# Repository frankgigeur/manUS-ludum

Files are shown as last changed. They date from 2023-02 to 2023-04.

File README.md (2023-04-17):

# ManUS Ludum

### Main robotisée et vision AI | UdeS-GRO
 

## Présentation du projet
L’objectif du projet est de concevoir la portion mécanique, électrique et informatique d’une main robotisée anthropomorphique pouvant actionner ses doigts pour jouer à roche-papier-ciseau. Une caméra vient en support à la main pour rendre le jeu encore plus interactif et réaliste.

gif &nbsp; &nbsp;gif

Les membres de l'équipe sont : <strong>Audrey Guy</strong>, <strong>Nicolaï Boudjack</strong>, <strong>Charles Ouellet</strong> et <strong>Alex Miville Deschênes</strong>.

GetImage
GetImage (1)
GetImage (2)
GetImage (3)

## Téléchargement et démarrage du projet
Pour télécharger le projet, il vous suffit de cloner le répertoire sur votre machine

1. Cloner le projet et l'enregistrer sur votre machine


2. Suivre les étapes des différentes sections du projet

> Interface de jeux et vision

> Électrique

> Mécanique

## Table des matières
* [Mécanique](/Mécanique#manUS-ludum)
	* [Fichiers CAD](https://github.com/frankgigeur/manUS-ludum/tree/main/M%C3%A9canique/CAD)
	* [Comment fabriquer ...](https://github.com/frankgigeur/manUS-ludum/tree/main/M%C3%A9canique#documentation-m%C3%A9canique)
		* [Liste des matériaux et composantes](https://github.com/frankgigeur/manUS-ludum/tree/main/M%C3%A9canique#liste-des-mat%C3%A9riaux-et-composantes)
		* [Fabrication des composantes](https://github.com/frankgigeur/manUS-ludum/tree/main/M%C3%A9canique#fabrication-des-composantes)
		* [Assemblage mécanique](https://github.com/frankgigeur/manUS-ludum/tree/main/M%C3%A9canique#assemblage-m%C3%A9canique)
*  [Électrique](/Électrique#manUS-ludum)
	* [Liste des matériaux et composantes](https://github.com/frankgigeur/manUS-ludum/tree/main/%C3%89lectrique#liste-des-mat%C3%A9riaux-et-composantes)
	* [Assemblage électrique](https://github.com/frankgigeur/manUS-ludum/tree/main/%C3%89lectrique#assemblage-%C3%A9lectrique)
* [Interface](/Interface%20Jeux#manUS-ludum)
	* [Logiciels requis](/Interface%20Jeux/README.md#installation-des-logiciels-recommandés)
	* [Dépendances](/Interface%20Jeux/README.md#Consolidation-des-versions-et-des-dépendances)
	* [Code de l'interface](/Interface%20Jeux/README.md#Comment-démarrer-linterface)
	* [Code de communication](/Interface%20Jeux/README.md#Comment-fonctionne-la-communication)
* [Vision](/Interface%20Jeux#manUS-ludum)
	* [Matériel nécessaire](/Interface%20Jeux/README.md#Matériel-nécessaire)
	* [Code de la reconnaissance visuelle](/Interface%20Jeux/README.md#Comment-fonctionne-la-reconnaissance-visuelle)
* [Arduino](https://github.com/frankgigeur/manUS-ludum/tree/main/Arduino/controle_servo)
* [Licence](/README.md#L43)

### Licence MIT
Copyright 2023 ManUS ludum

Permission is hereby granted, free of charge, to any person obtaining a copy of this software and associated documentation files (the "Software"), to deal in the Software without restriction, including without limitation the rights to use, copy, modify, merge, publish, distribute, sublicense, and/or sell copies of the Software, and to permit persons to whom the Software is furnished to do so, subject to the following conditions:

The above copyright notice and this permission notice shall be included in all copies or substantial portions of the Software.

THE SOFTWARE IS PROVIDED "AS IS", WITHOUT WARRANTY OF ANY KIND, EXPRESS OR IMPLIED, INCLUDING BUT NOT LIMITED TO THE WARRANTIES OF MERCHANTABILITY, FITNESS FOR A PARTICULAR PURPOSE AND NONINFRINGEMENT. IN NO EVENT SHALL THE AUTHORS OR COPYRIGHT HOLDERS BE LIABLE FOR ANY CLAIM, DAMAGES OR OTHER LIABILITY, WHETHER IN AN ACTION OF CONTRACT, TORT OR OTHERWISE, ARISING FROM, OUT OF OR IN CONNECTION WITH THE SOFTWARE OR THE USE OR OTHER DEALINGS IN THE SOFTWARE.

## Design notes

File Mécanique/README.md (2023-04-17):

# Documentation-Mécanique

## Fichiers ['CAD'](./CAD/)
Les fichiers suivants contiennent les CAD nécessaires à la ['fabrication'](##Fabrication%20des%20composantes) des composantes mécaniques du projet.

- [ ]  [`Doigts`](./CAD/Doigts/), [`Paume`](./CAD/Paume%20et%20poignet//), [`Poignet`](./CAD/Paume%20et%20poignet//) <br>
- [ ]  [`Ligaments`](./CAD/Ligaments/) <br>
- [ ]  [`Support moteur`](./CAD/Moteurs%20support%20et%20poulies/), [`Poulies moteurs`](./CAD/Moteurs%20support%20et%20poulies/) <br>
- [ ]  [`Support arbre`](./CAD/M%C3%A9canisme%20redirection%20fils/), [`Poulies arbre`](./CAD/M%C3%A9canisme%20redirection%20fils/), [`Support supérieur`](./CAD/M%C3%A9canisme%20redirection%20fils/) <br>
- [ ]  [`Base`](./CAD/Plaque%20montage/) <br>

## Liste des matériaux et composantes
- [ ] &nbsp;Vis autoperçantes M1.2 x 3mm <br>
- [ ] &nbsp;Vis M3 x 20mm <br>
- [ ] &nbsp;Vis M3 x 45mm <br>
- [ ] &nbsp;Vis M5 x 10mm <br>
- [ ] &nbsp;Vis M5 x 50mm <br>
- [ ] &nbsp;12 x 12 x 1/8 po. Acrylique <br>
- [ ] &nbsp;Feuille de nylon cordura 1000D [(Club Tissu)](https://www.clubtissus.com/fr/nylon-cordura-1000d-noir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) <br>
- [ ] &nbsp;Mica plastique transparent 20 ga (Club Tissu) <br>
- [ ] &nbsp;Aggraphe à papier <br>
- [ ] &nbsp;Arbre de métal 5mm x 100mm [(Amazon)](https://www.amazon.ca/dp/B01B27MJC6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) <br>
- [ ] &nbsp;Bearing à billes 5mm x 11mm x 4mm [(Amazon)](https://www.amazon.ca/dp/B07GBTWLCZ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) <br>
- [ ] &nbsp;Fil de pêche 80 lbs <br>
- [ ] &nbsp;Goupille (dowel pin) 1/8 x 0.5 po. <br> 
- [ ] &nbsp;Servomoteur HS-422 Hitec [(Robotshop)](https://ca.robotshop.com/fr/products/hitec-hs-422-servo-motor) <br>

## Fabrication des composantes
avant bras v1

La fabrication des composantes du projet nécessite l'accès à **une découpeuse laser**, **une imprimante 3D** et d'un **fer à souder**. 
Les étapes suivantes permmettent de fabriquer l'ensemble des composantes mécaniques du projets selon les étapes suivantes:

1. Impression des doigts du dossier [`Doigts`](./CAD/Doigts/) en PLA à l'aide d'une imprimante 3D (Infill minimum 80%).

2. Impression de la paume et de son support de type poignet dans le dossier [`Paume et poignet`](./CAD/Paume%20et%20poignet//) (Infill minimum 40%).

3. Impression des [`poulies de servo moteurs`](./CAD/Moteurs%20support%20et%20poulies/)  ( **x5** ), du [`support à moteurs`](./CAD/Moteurs%20support%20et%20poulies/), des [`poulies inserés sur les paliers à billes`](./CAD/M%C3%A9canisme%20redirection%20fils/) ( **x12** ) et des [`supports à arbre types 1 et 2`](./CAD/M%C3%A9canisme%20redirection%20fils/) ( **x4 chaque** ).

4. Découpe du [`support supérieur de la main`](./CAD/M%C3%A9canisme%20redirection%20fils/) en acrylique à l'aide d'une découpeuse laser.

4. Découpe des [`ligaments`](./CAD/Ligaments/) en nylon des différents doigts ( **2 par doigts** ) à l'aide de la découpeuse laser.

5. Découpe des [`ligaments`](./CAD/Ligaments/) en mica des différents doigts ( **3 par doigts** ) à l'aide de ciseaux.

6. Découpe des fils de pêche ≈ 60cm ( **x10** ).

7. Découpe de la [`base`](./CAD/Plaque%20montage/) en acrylique du support de la main à l'aide d'une découpeuse laser. 

## Assemblage mécanique
Pour l'assemblage des pièces mécaniques, se fier aux [`assemblages complets`](./CAD/Assemblages%20complets/) fournis ainsi qu'aux [`dessins`](./Dessins/), [images](https://github.com/frankgigeur/manUS-ludum/tree/main/Images) fournies et explications ultérieures.

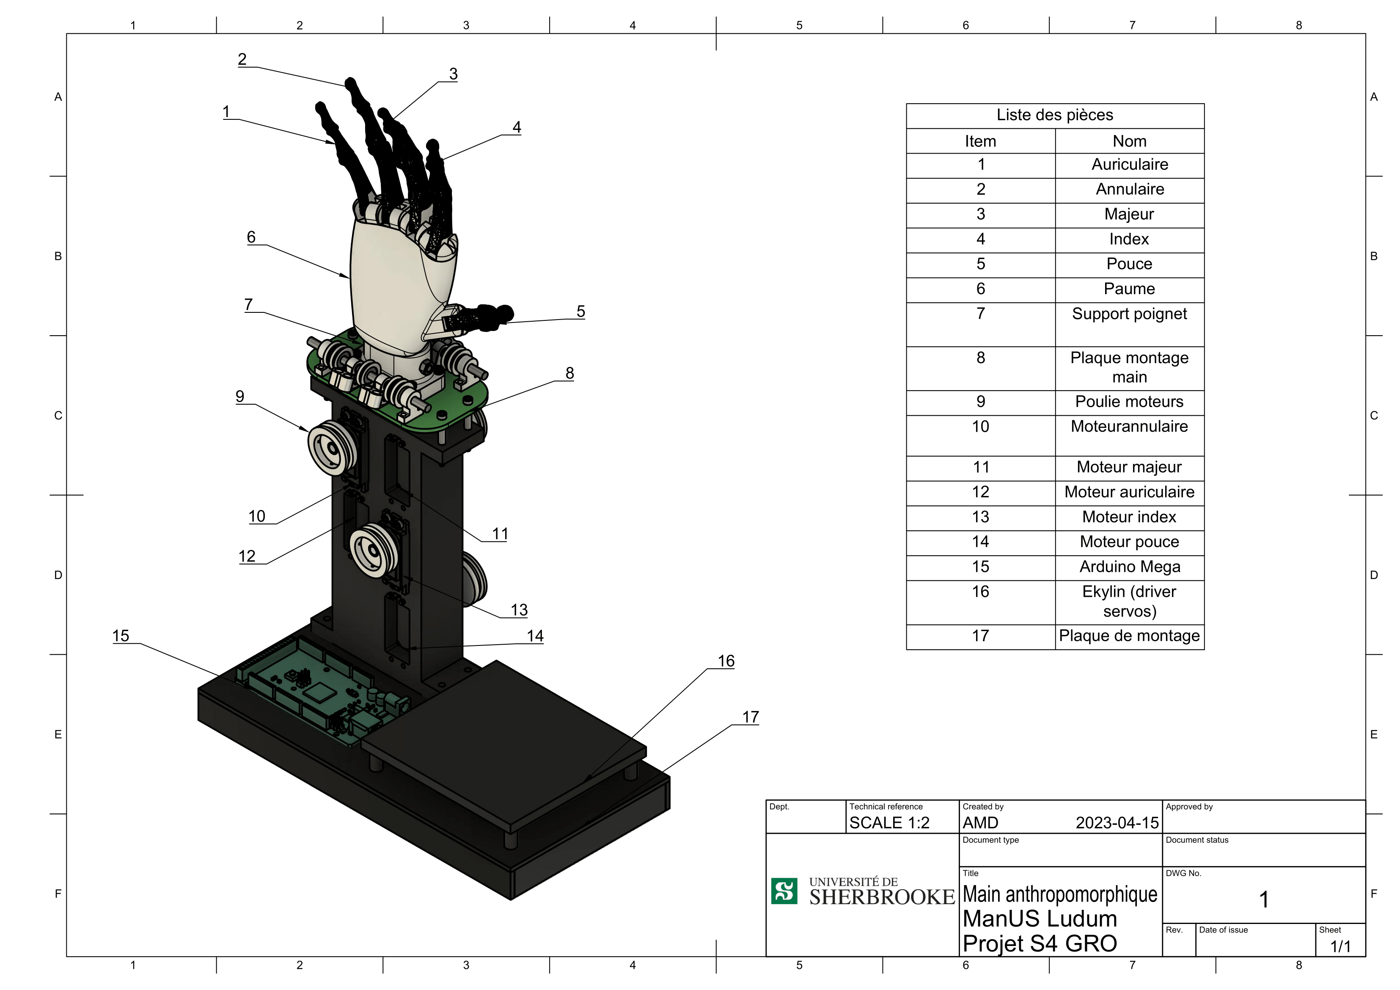
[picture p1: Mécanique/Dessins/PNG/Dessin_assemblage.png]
Dessin assemblage


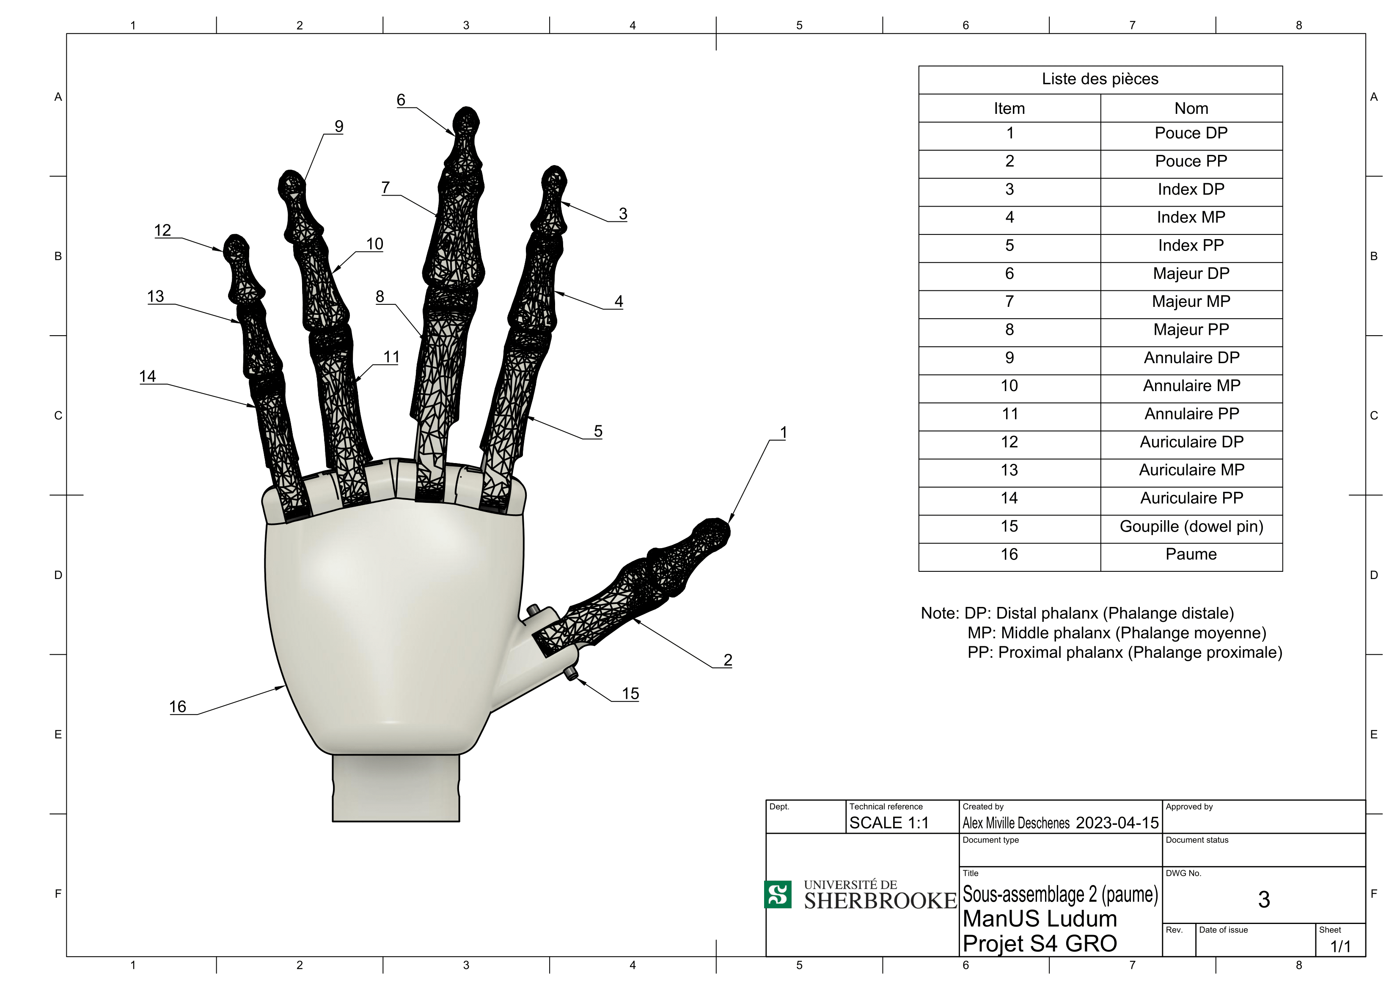
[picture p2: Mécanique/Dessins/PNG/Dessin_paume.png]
Dessin paume


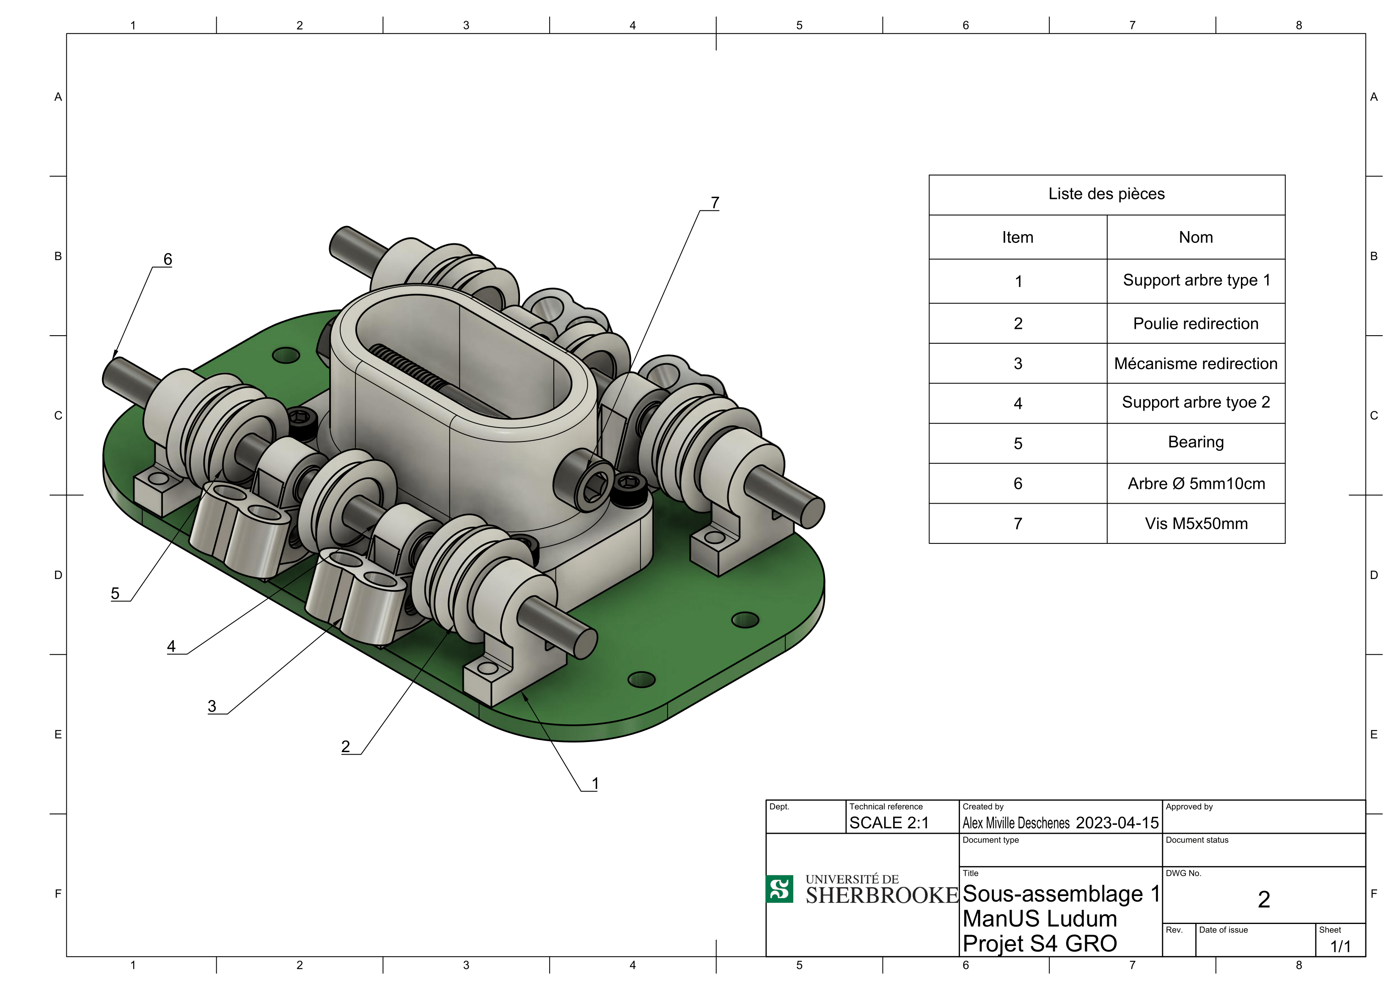
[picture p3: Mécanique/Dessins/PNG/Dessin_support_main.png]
Dessin redirection fils


### **Montage des doigts**
Pour le montage des doigts, il est nécesaire d'insérer les ligamants aux points d'insertion anatomique selon la figure suivante:
exemple ligament

Pour se faire, faire fondre les vis m1.2 aux points cibles et visser par la suite celles-ci avec les ligaments de mica et de nylon. La figure suivante présente le nom des ligaments à utiliser selon la jonction entre les ossements.

nom ligaments

La jonction MCPP est une superposition de ligaments de mica et de nylon, tandis que la jonction PPMP est seulement un ligament de nylon. Aussi, à noter que cette figure présente le montage de l'index, mais la même procédure s'applique pour tous les autres doigts. <br> <br>

Finalement, les poulies et les tendons peuvent être installés. Les aggraphes peuvent donc être pliées et coupées pour ensuite être insérées dans le doigt à l'aide d'un fer à souder. La figure suivante présente le positionnement des poulies (voir la section [Montage des poulies sur la paume](#montage-des-poulies-sur-la-paume))

### Montage des doigts sur la paume
Une fois les doigts assemblés, il faut les placer sur la paume. Pour se faire, on glisse la goupille (dowel pin) dans le trou situé sur la phalange proximale du doigt de manière à ce que celle-ci dépasse également de chaque côté.

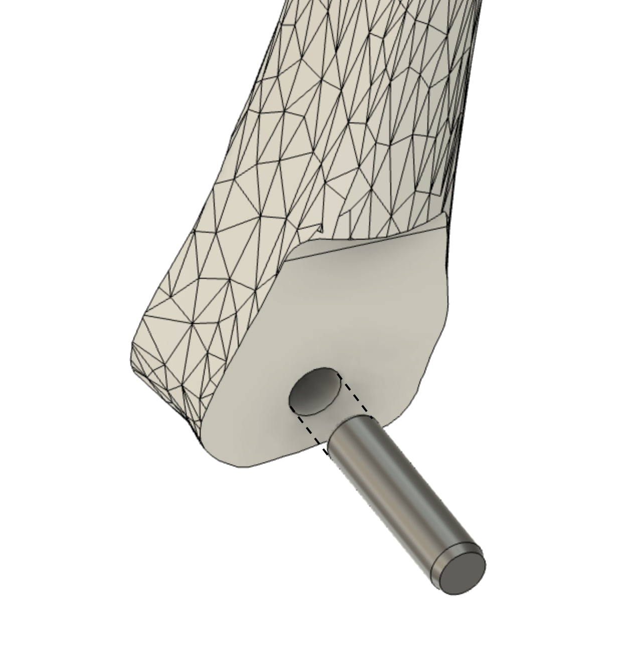
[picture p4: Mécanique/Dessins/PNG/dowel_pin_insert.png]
dowel insert


Ensuite, on force le doigt avec la goupille dans chacune des positions de la paume pour les doigts correspondants. Une grande force pourrait être nécessaire.

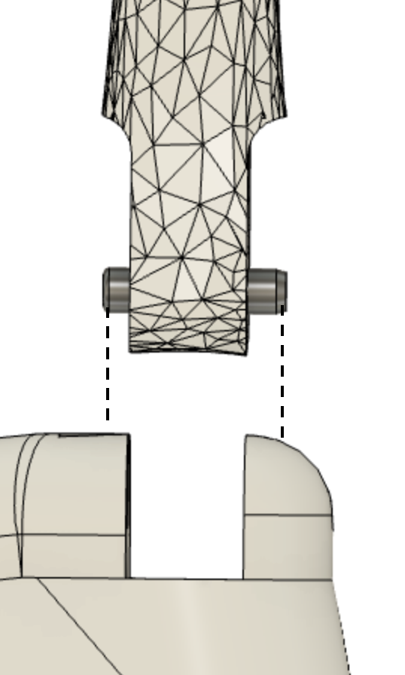
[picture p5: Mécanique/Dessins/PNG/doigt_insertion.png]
finger insert


### Montage des poulies sur la paume

Se fier à l'image suivante pour le montage des poulies de redirection des fils (agrafes à papier) sur la paume ainsi que le point de départ du fil de pêche:

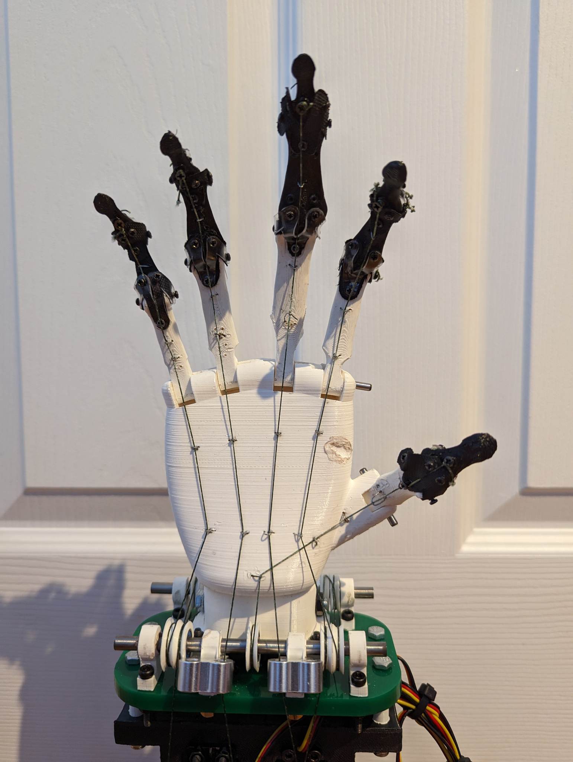
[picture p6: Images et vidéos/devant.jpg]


### Redirection des fils

Une fois la main assemblée et les poulies installées, il faut rediriger le fil de pêche vers les servomoteurs. La figure suivante montre la redirection du fil pour le petit doigt. Les flèches rouges sont associés au fil du devant et les flèches bleues au fil du derrière. De plus, le fil est enroulé une fois autour des poulies pour s'assurer qu'il ne sorte pas lors du mouvement.
CDhd5bslpE


Il est à noté que la redirection des fils de chaque doigt suit le même modèle que celui du petit doigt. Il suffit alors de reproduire pour chaque doigt.

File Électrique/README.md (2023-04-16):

# Documentation ManUS Ludum - Électrique

## Liste des matériaux et composantes
- [ ] &nbsp;Arduino Mega 2560  [(Arduino)](https://ca.robotshop.com/fr/products/hitec-hs-422-servo-motor) <br>
- [ ] &nbsp;Module PCA9685 [(Adafruit)](https://learn.adafruit.com/16-channel-pwm-servo-driver?view=all) <br>
- [ ] &nbsp;Connecteurs mâle-femelle type "jumper" (**x4**) <br>
- [ ] &nbsp;Alimentation 12V <br>
- [ ] &nbsp;Câble USB type A/B <br>

## Assemblage électrique
L'assemblage électrique du projet se résume aux étapes suivantes en se basant sur le schéma électrique suivant : 

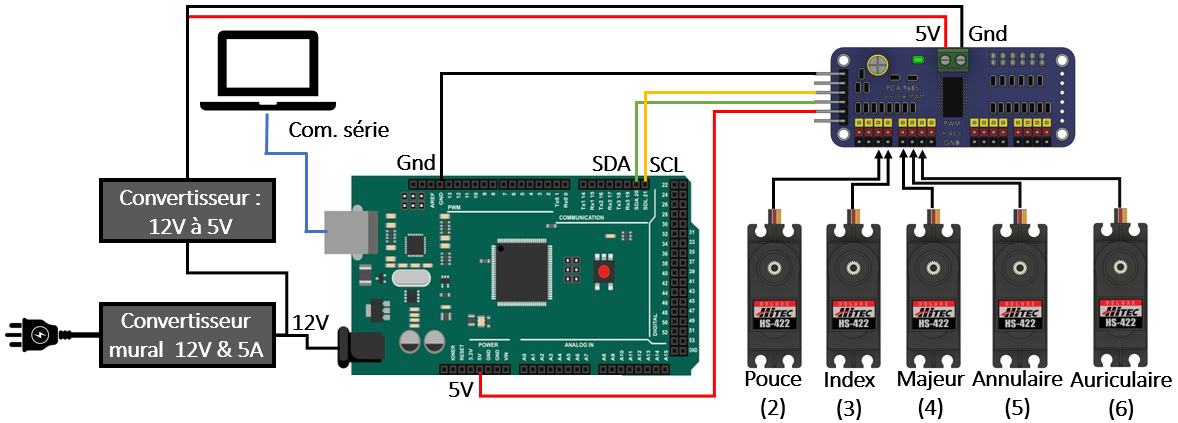
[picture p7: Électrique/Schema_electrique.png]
Schema electrique


1. Connecter les fils 5V, GND, SDA, SCL de l'Arduino au module PCA9685 selon le schéma ci-haut à l'aide des connecteurs mâle-femelle.

2. Connecter les fils des servomoteurs au module PCA9685 selon le schéma électrique en s'assurant de les placer dans le bon sens (bien regarder que le fil noir du servomoteur soit connecté au GND du module).

3. Connecter le convertisseur 12V à 5V au module PCA9685 toujours selon le schéma électrique.

4. Connecter l'alimentation 12V au Arduino et au convertisseur 12V à 5V.

5. Connecter le câble USB type A/B au Arduino ainsi qu'à l'ordinateur.

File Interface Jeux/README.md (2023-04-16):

# Documentation-Interface

# Matériel nécessaire
- [ ] Caméra (intégré à un ordinateur portable ou une webcam)
- [ ] ArduinoMEGA 2560

# Installation des logiciels recommandés
- [ ] PyCharm
 ```
 https://www.jetbrains.com/pycharm/download/#section=windows
 ```
- [ ] QtDesigner
 ```
 https://build-system.fman.io/qt-designer-download
 ```

# Consolidation des versions et des dépendances
Ce projet fonctionne avec Python 3.7 ou 3.10, mais il est bon de noter que les dépendances décrites ci-dessous s'appliquent à un environnement python 3.10.

## Installation des librairies et interpréteur
Pour commencer, installez python sur votre machine.
Ensuite, dans PyCharm, vous allez ajouter les librairies nécessaires à votre interpréteur en vous fiant aux étapes suivantes:

1. À partir de l'onglet "File" sélectionner "Settings"

2. Sous "Projet", sélectionner "Python Interpreter"

3. Choisir la version de python sur laquelle vous souhaitez installer vos librairies
 
4. En appuyant sur le bouton +, choissisez les librairies selon les requis énumérés ci-dessous et cliquez sur "Install Package"


## Liste des librairies à installer
- [ ] opencv-contrib-python == 4.3.0
- [ ] scikit-learn == 0.11
- [ ] tensorflow == 2.2.0
- [ ] numpy == 1.18.3
- [ ] matplotlib == 3.1.0
- [ ] scipy == 1.4.1
- [ ] PyQt5 == 5.15.9

S'il y a des erreurs de compilation, fiez-vous aux messages d'erreurs de la console et installez les librairies manquantes!

# Comment démarrer l'interface
Pour lancer et ou modifier l'interface, le fichier de code est InterfaceJeux.py .
Pour démarrer l'interface il suffit, dans PyCharm, d'appuyer sur le bouton "Run".



L'interface comprends des boutons de contrôle de la main, une rétroaction temps réel de la caméra, un décompte de jeux et des statistiques.



# Comment fonctionne la reconnaissance visuelle
Pour entraîner un nouveau modèle de reconnaissance visuelle, utilisez le fichier /ModeleVision/modelTraining.py .
Dans ce fichier, en vous fiant aux commentaires, vous serez en mesure de changer les différents paramètres du modèle
et d'entraîner votre propre modèle. Ensuite, dans le fichier algoRPC du dossier principal, vous n'aurez qu'à changer 
le nom du modèle à télécharger et à vous assurer que le dit modèle se trouve dans le dossier.



# Comment fonctionne l'algorithme décisionnel de jeux
De base, l'ordinateur jouera des coups aléatoires. Cependant, il est possible de le faire jouer avec un algorithme décisionnel
de type chaînes de Markov. Le code responsable des calculs statistiques derrrière les prédictions des chaînes est dans le fichier RPCmarkov.py

# Comment fonctionne la communication
La communication entre l'ordinateur et le microcontrôleur Arduino se fait par série avec le fichier CommWorker.py
Ce code produit une rétroaction à la console permettant à l'utilisateur de comprendre les commandes envoyées à la main.



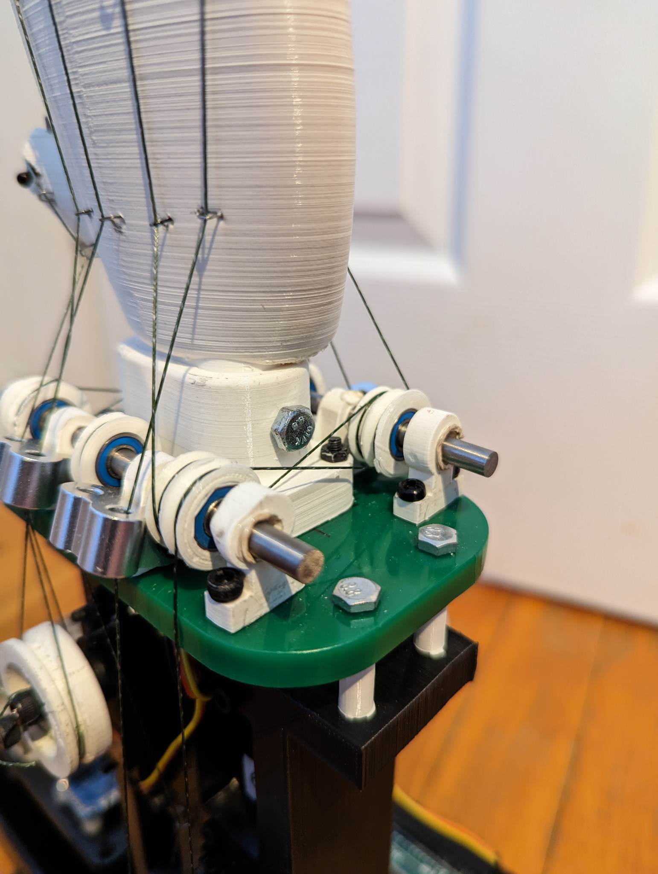
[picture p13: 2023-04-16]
Images et vidéos/poulies_redirection.jpg

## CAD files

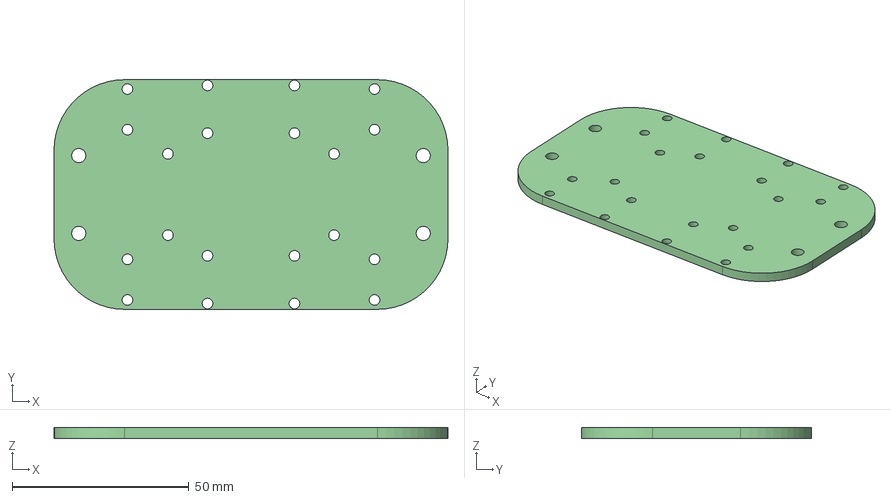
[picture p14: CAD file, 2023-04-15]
Mécanique/CAD/Mécanisme redirection fils/Plaque_montage_main.step
111.5 x 65.0 x 3.00 mm

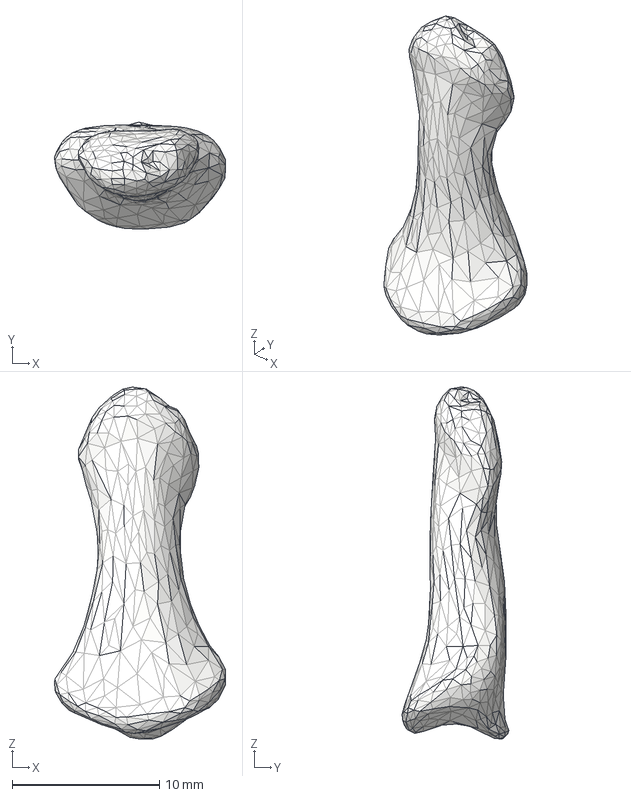
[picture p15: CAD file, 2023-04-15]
Mécanique/CAD/Doigts/Annulaire/STEP/Annulaire_DP.step
11.6 x 7.27 x 23.9 mm

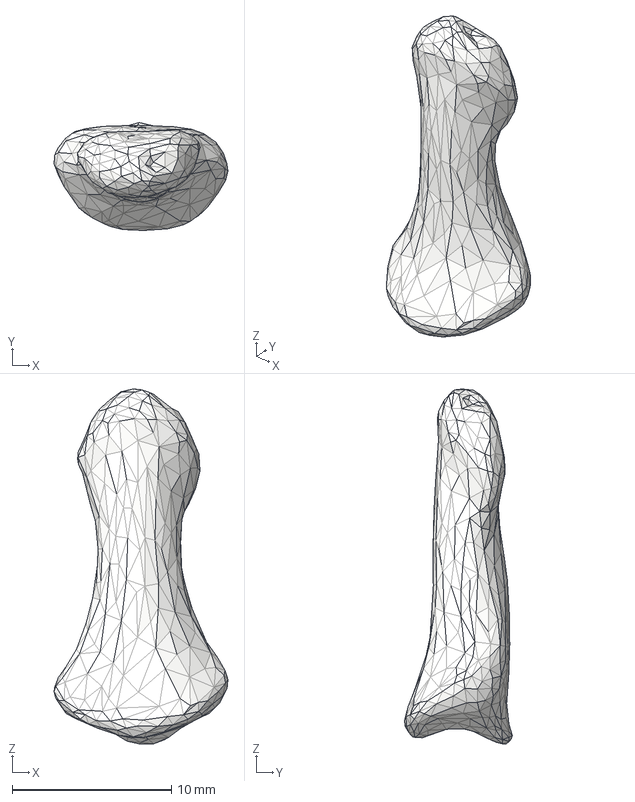
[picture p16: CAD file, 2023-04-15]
Mécanique/CAD/Doigts/Auriculaire/STEP/Auriculaire_DP.step
10.9 x 6.78 x 22.3 mm

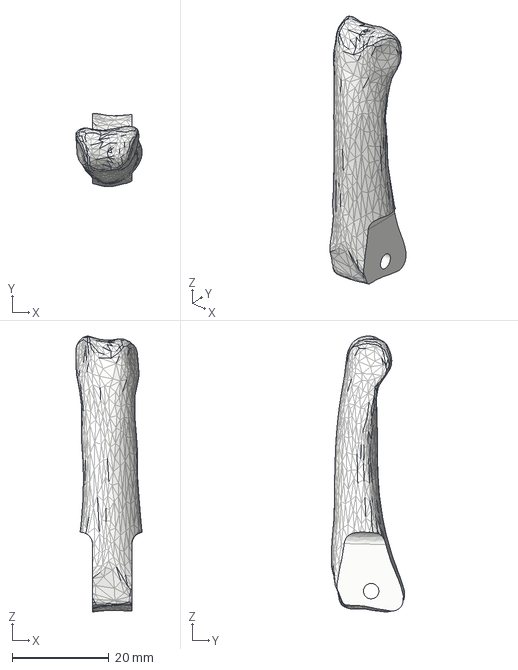
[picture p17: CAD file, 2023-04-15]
Mécanique/CAD/Doigts/Index/STEP/IndexPP.step
13.6 x 15.2 x 56.9 mm

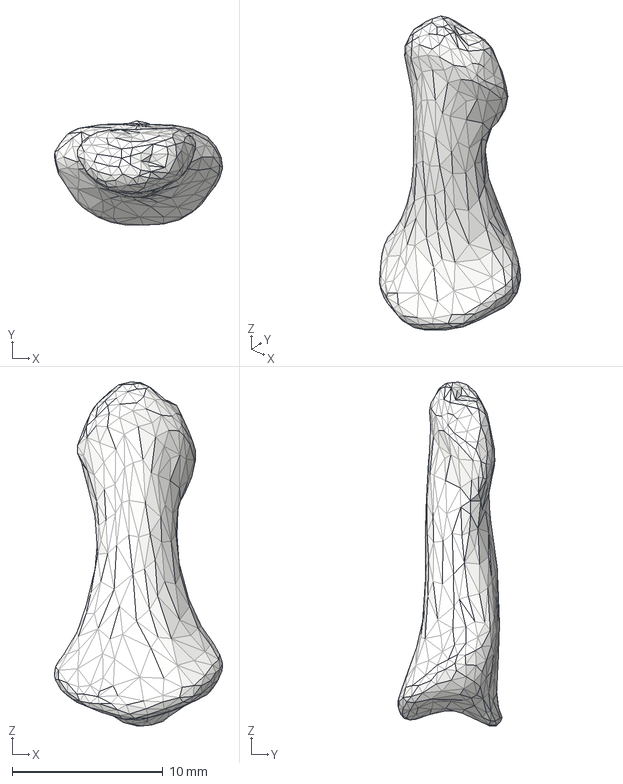
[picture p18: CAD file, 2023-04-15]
Mécanique/CAD/Doigts/Majeur/STEP/Majeur_DP.step
11.2 x 6.93 x 22.8 mm

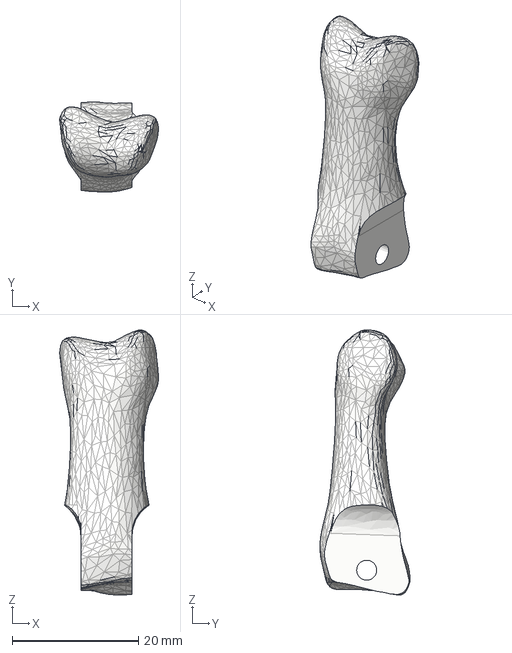
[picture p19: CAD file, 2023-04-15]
Mécanique/CAD/Doigts/Pouce/STEP/Pouce_PP.step
15.7 x 14.3 x 42.0 mm

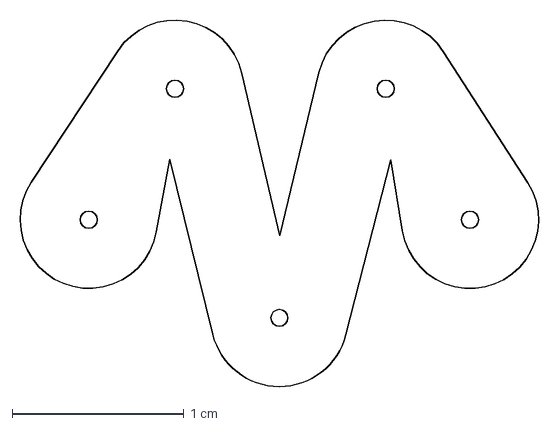
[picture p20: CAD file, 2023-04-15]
Mécanique/CAD/Ligaments/Universal DPMP Ligament.dxf
3.07 x 2.16 cm

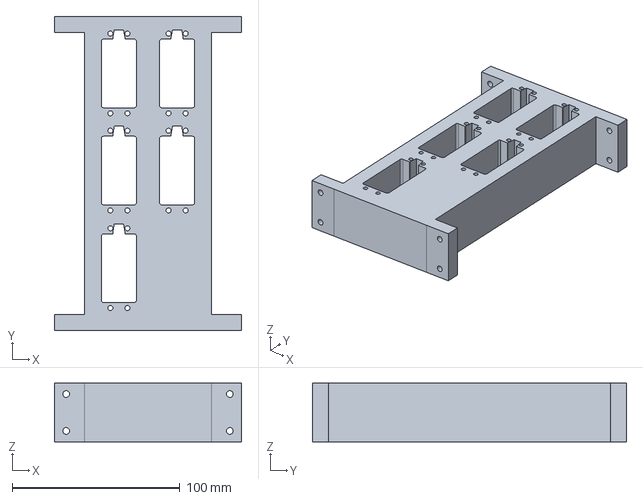
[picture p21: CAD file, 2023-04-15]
Mécanique/CAD/Moteurs support et poulies/Support_moteurs.step
111.5 x 187.0 x 35.0 mm

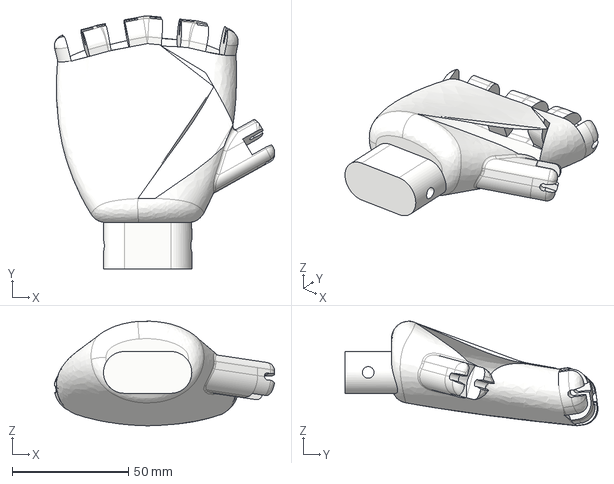
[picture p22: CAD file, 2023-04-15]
Mécanique/CAD/Paume et poignet/Paume.step
95.0 x 109.0 x 45.1 mm

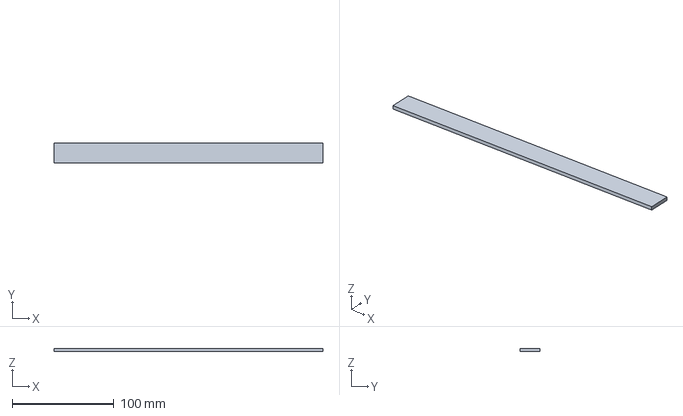
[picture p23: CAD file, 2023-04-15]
Mécanique/CAD/Plaque montage/Plaque_montage_devant_arriere.step
265.0 x 20.0 x 3.17 mm

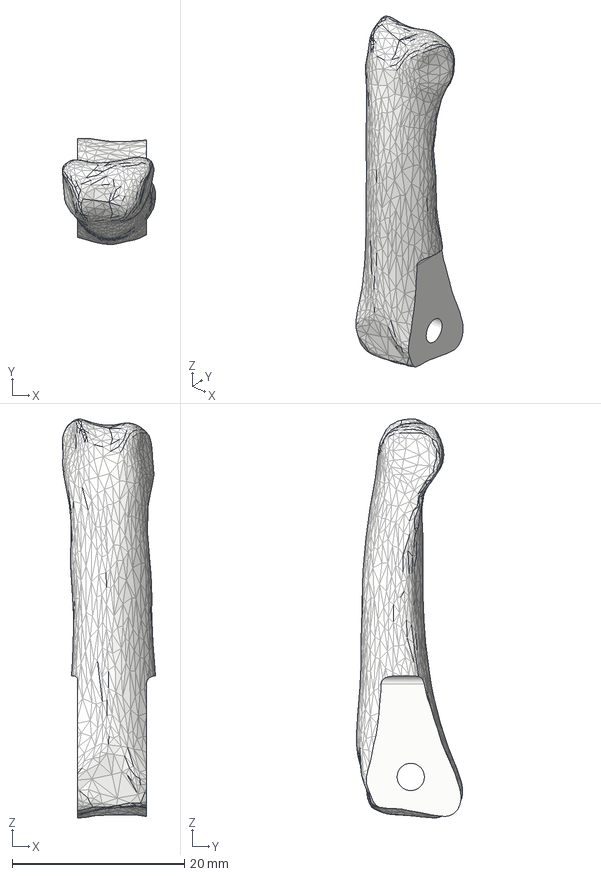
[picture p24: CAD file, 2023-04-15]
Mécanique/CAD/Doigts/Auriculaire/STEP/Auriculaire_PP.step
10.8 x 12.3 x 46.3 mm

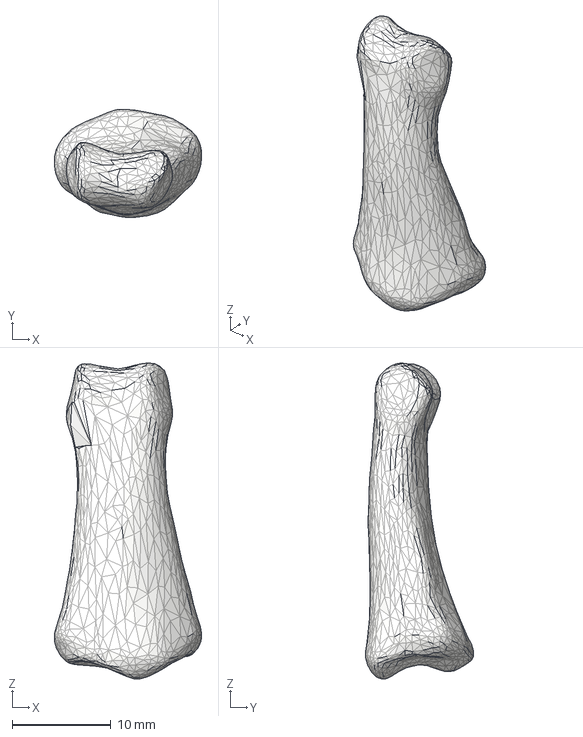
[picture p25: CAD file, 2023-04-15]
Mécanique/CAD/Doigts/Index/STEP/IndexMP.step
15.0 x 11.0 x 32.1 mm

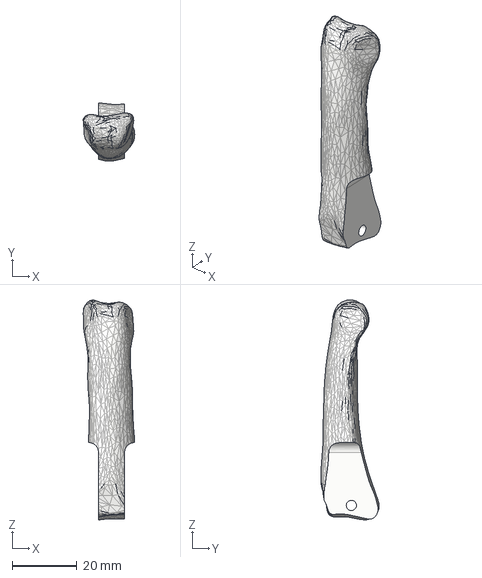
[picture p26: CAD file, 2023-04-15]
Mécanique/CAD/Doigts/Majeur/STEP/Majeur_PP.step
16.0 x 18.1 x 68.1 mm

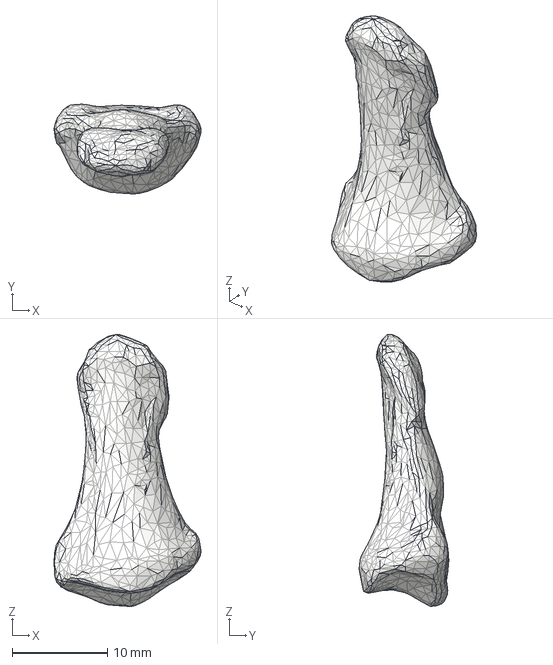
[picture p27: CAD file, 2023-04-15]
Mécanique/CAD/Doigts/Pouce/STEP/Pouce_DP.step
15.4 x 9.41 x 28.5 mm

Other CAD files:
Mécanique/CAD/Doigts/Annulaire/STEP/Annulaire_PP.step
Mécanique/CAD/Ligaments/Ring PPMP Ligament.dxf
Mécanique/CAD/Moteurs support et poulies/Poulies_moteurs.step
Mécanique/CAD/Mécanisme redirection fils/Support_arbre_type2.step
Mécanique/CAD/Doigts/Annulaire/STEP/Annulaire_MP.step
Mécanique/CAD/Doigts/Auriculaire/STEP/Auriculaire_MP.step
Mécanique/CAD/Doigts/Index/STEP/IndexDP.step
Mécanique/CAD/Doigts/Majeur/STEP/Majeur_MP.step
Mécanique/CAD/Ligaments/Index PPMP Ligament.dxf
Mécanique/CAD/Ligaments/Middle PPMP Ligament.dxf
Mécanique/CAD/Ligaments/Pinky PPMP Ligament.dxf
Mécanique/CAD/Ligaments/Thumb PPDP ligament.dxf
Mécanique/CAD/Mécanisme redirection fils/Poulie.step
Mécanique/CAD/Mécanisme redirection fils/Redirecteur_fils.step
Mécanique/CAD/Mécanisme redirection fils/Support_arbre_type1.step
Mécanique/CAD/Paume et poignet/Support_poignet.step
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

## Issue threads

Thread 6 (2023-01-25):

Test(communication et algorithme de jeux)

frankgigeur, 2023-01-25:

AudreyGuy, 2023-03-15:
4h - Algorithme de base fait, il faut l'inclure à l'interface et le lier au décompte.

AudreyGuy, 2023-04-17:
Tests concluant, communication finale le 29 mars. Fermeture du billet par Audrey Guy

Closed 2023-04-17.

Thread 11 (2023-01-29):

Interface de jeux

AudreyGuy, 2023-01-29:

AudreyGuy, 2023-02-15:
11 février - travail 12h, première itération terminée, tous les boutons sont fonctionnels. Je passe à la communication!

AudreyGuy, 2023-04-17:
Itération finale le 12 avril, ajout des dernières fonctionnalités, francisation et ajustement des étiquettes. Fermeture du billet par Audrey Guy

Closed 2023-04-17.

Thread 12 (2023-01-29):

Communication vision/main

AudreyGuy, 2023-01-29:

AudreyGuy, 2023-02-21:
6h mercredi le 15 février, il reste à tester avec l'open-CR et les moteurs

AudreyGuy, 2023-03-13:
6h dimanche 12 mars, communication réussie avec l'interface et un Arduino, passage aux tests avec moteurs

AudreyGuy, 2023-04-17:
Itération finale le 29 mars, dernier débogage et autres ajustements. Fermeture du billet par Audrey Guy

Closed 2023-04-17.

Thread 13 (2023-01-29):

Entraînement du modèle de reconnaissance visuelle

AudreyGuy, 2023-01-29:

AudreyGuy, 2023-03-15:
4h - Modèle entraîné et testé dans l'environnement de la classe. Efficacité d'environ 99% sur la détection.

AudreyGuy, 2023-04-17:
Itération finale de l'entraînement le 29 mars. Fermeture du billet par Audrey Guy

Closed 2023-04-17.

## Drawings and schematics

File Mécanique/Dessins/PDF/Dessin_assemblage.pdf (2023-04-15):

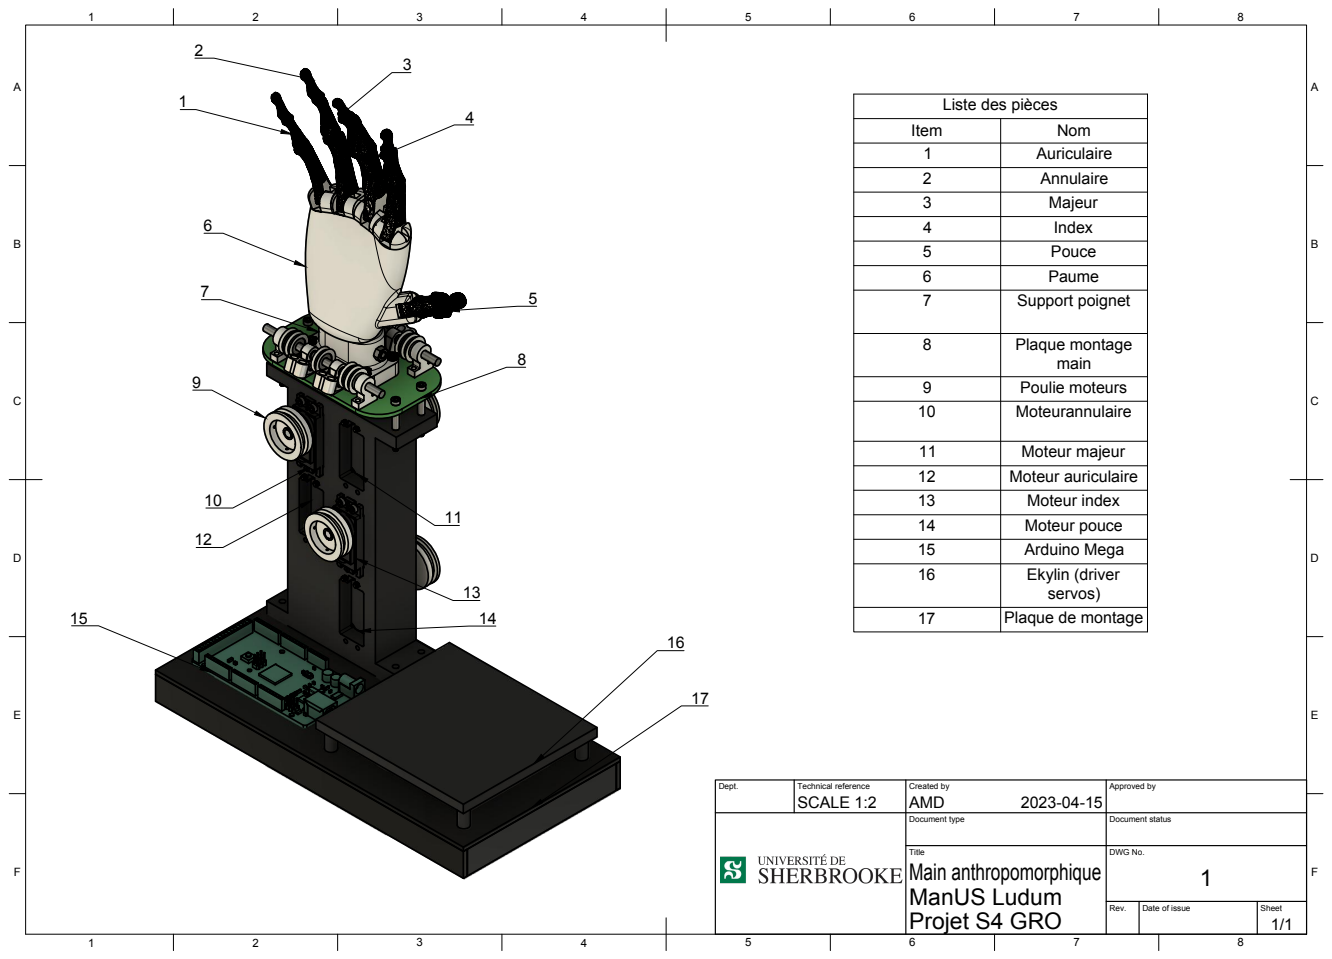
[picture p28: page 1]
Dept.; Technical reference; Created by; Approved by; Document type; Document status; Title; DWG No.; Rev.; Date of issue; Sheet; Projet S4 GRO; ManUS Ludum; Main anthropomorphique; SCALE 1:2; AMD 1 A; 8 BCDEF; ABCDEF 1 2; Item; Nom 1; Auriculaire 2; Annulaire 3; Majeur 4; Index 5; Pouce 6; Paume 7; Support poignet 8; Plaque montage; main 9; Poulie moteurs; Moteur majeur; Moteur auriculaire; Moteur index; Moteur pouce; Arduino Mega; Ekylin (driver; Plaque de montage

Liste des pièces

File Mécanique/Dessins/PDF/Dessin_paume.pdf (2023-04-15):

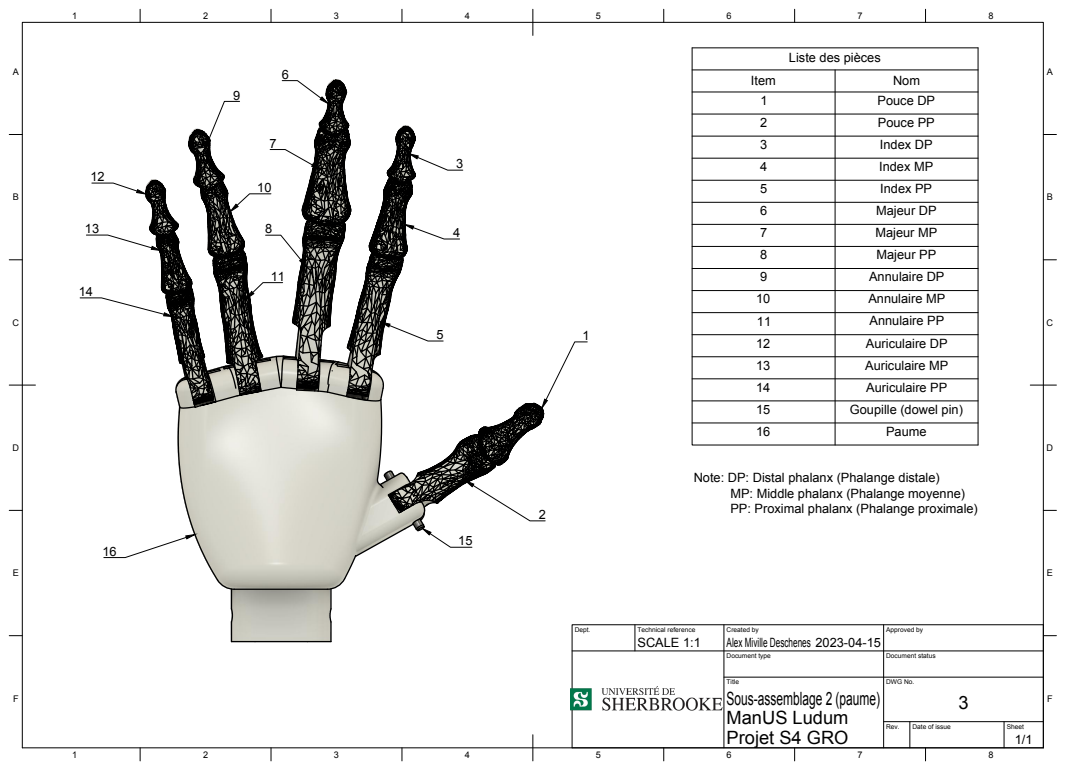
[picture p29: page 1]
8 BCDEF; ABCDEF; Dept.; Technical reference; Created by; Approved by; Document type; Document status; Title; DWG No.; Rev.; Date of issue; Sheet; Projet S4 GRO; ManUS Ludum; Sous-assemblage 2 (paume); SCALE 1:1; Alex Miville Deschenes 1 2 5 34 6 78 9; Item; Nom 1; Pouce DP 2; Pouce PP 3; Index DP 4; Index MP 5; Index PP 6; Majeur DP 7; Majeur MP 8; Majeur PP 9; Annulaire DP; Annulaire MP; Annulaire PP; Auriculaire DP; Auriculaire MP; Auriculaire PP; Goupille (dowel pin)

Liste des pièces

Note: DP: Distal phalanx (Phalange distale)

MP: Middle phalanx (Phalange moyenne)
PP: Proximal phalanx (Phalange proximale)

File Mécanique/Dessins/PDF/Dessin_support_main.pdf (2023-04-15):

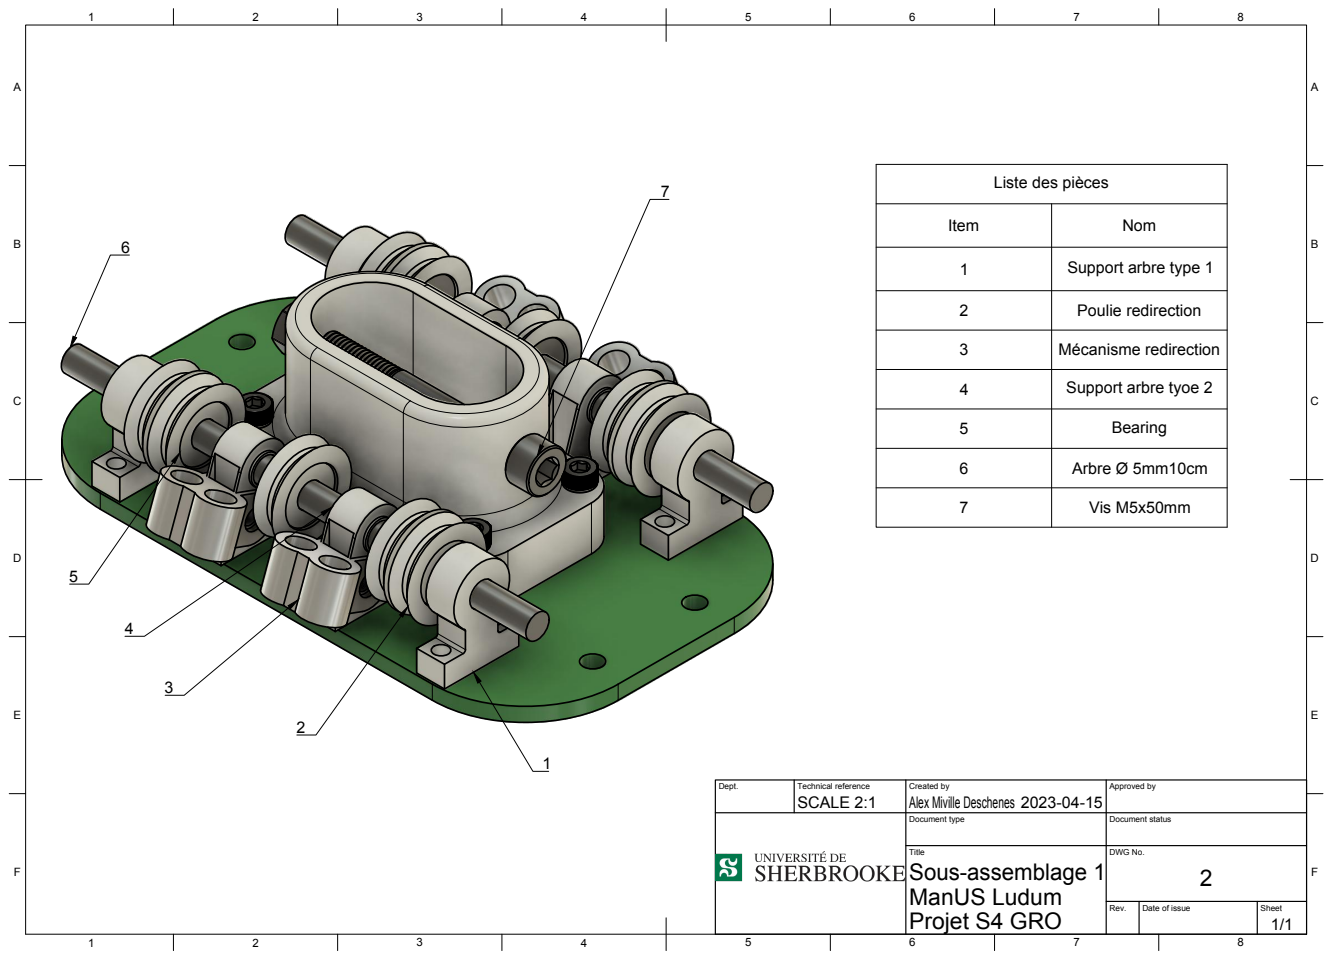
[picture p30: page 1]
Title; DWG No.; Rev.; Date of issue; Sheet; Projet S4 GRO; ManUS Ludum; Sous-assemblage 1

Liste des pièces

Item | Nom

1 | Support arbre type 1

2 | Poulie redirection

3 | Mécanisme redirection

4 | Support arbre tyoe 2

5 | Bearing

6 | Arbre Ø 5mm10cm

7 | Vis M5x50mm

Dept. | Technical reference SCALE 2:1 | Created by Alex Miville Deschenes 2023-04-15 | Approved by

Document type | Document status

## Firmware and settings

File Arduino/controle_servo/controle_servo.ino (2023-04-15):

#include "define.h"
#include <Wire.h>
#include <Adafruit_PWMServoDriver.h>

void roche();
void papier();
void ciseau();
void cold_stop();
void initial();

// called this way, it uses the default address 0x40
Adafruit_PWMServoDriver pwm = Adafruit_PWMServoDriver();

const byte numChars = 64;
char receivedChars[numChars];
bool newData = false;
void replyToUi();
void recvWithStartEndMarkers() ;

void setup() {

  Serial.begin(115200);

  //Serial.println("<Arduino is ready>");

  pwm.begin();
  pwm.setOscillatorFrequency(PCA9685_OSC_FREQ);
  pwm.setPWMFreq(HS422_SERVO_FREQ);
  cold_stop();
  delay(3000);  
}


void loop() {

  recvWithStartEndMarkers();
  replyToUi();
  //  roche();
  //  delay(3000);  
  //  initial();
  //  delay(3000);  
  //  papier();
  //  delay(3000);  
  //  initial();
  //  delay(3000);
  //  ciseau();
  //  delay(3000);  
  //  initial();
  //  delay(3000);
}

void recvWithStartEndMarkers() {
    static boolean recvInProgress = false;
    static byte ndx = 0;
    char startMarker = '<';
    char endMarker = '>';
    char lastReadChar;
    while (Serial.available() > 0 && newData == false) {
        lastReadChar = Serial.read();
        if (recvInProgress) {
            if (lastReadChar != endMarker) {
                receivedChars[ndx] = lastReadChar;
                ndx++;
                if (ndx >= numChars) {
                    ndx = numChars - 1;
                }
            }
            else {
                receivedChars[ndx] = '\0'; // terminate the string
                recvInProgress = false;
                ndx = 0;
                newData = true;
            }
        }
        else if (lastReadChar == startMarker) {
            recvInProgress = true;
        }
    }
}
void replyToUi(){
  if(newData){
        switch(receivedChars[0])
        {
          case 'I':
            initial();
            Serial.println("<initial>");
            break;
          case 'R':
            roche();
            Serial.println("<roche>");
            break;
          case 'C':
            ciseau();
            Serial.println("<ciseaux>");  
            break;
          case 'P':
            papier();
            Serial.println("<papier>");
            break;
          case 'A':
            Serial.println("<arret>");
            cold_stop();
            break;
          default:
            break;
        }
        newData = false;
      }
}

void initial()
{
  pwm.setPWM(ID_petitdoigt, 0, HS422_pd_inc_init);
  pwm.setPWM(ID_annulaire, 0, HS422_an_inc_init);
  pwm.setPWM(ID_majeur, 0, HS422_ma_inc_init);
  pwm.setPWM(ID_index, 0, HS422_in_inc_init);
  pwm.setPWM(ID_pouce, 0, HS422_po_inc_init);
}

void roche()
{
  pwm.setPWM(ID_pouce, 0, HS422_po_inc_comp);
  delay(30);
  pwm.setPWM(ID_petitdoigt, 0, HS422_pd_inc_comp);
  pwm.setPWM(ID_annulaire, 0, HS422_an_inc_comp);
  pwm.setPWM(ID_majeur, 0, HS422_ma_inc_comp);
  pwm.setPWM(ID_index, 0, HS422_in_inc_comp);
 
}

void papier()
{
  pwm.setPWM(ID_petitdoigt, 0, HS422_pd_ext_comp);
  pwm.setPWM(ID_annulaire, 0, HS422_an_ext_comp);
  pwm.setPWM(ID_majeur, 0, HS422_ma_ext_comp);
  pwm.setPWM(ID_index, 0, HS422_in_ext_comp);
  pwm.setPWM(ID_pouce, 0, HS422_po_ext_comp);
}

void ciseau()
{
  pwm.setPWM(ID_petitdoigt, 0, HS422_pd_inc_comp);
  pwm.setPWM(ID_annulaire, 0, HS422_an_inc_comp);
  pwm.setPWM(ID_majeur, 0, HS422_ma_ext_comp);
  pwm.setPWM(ID_index, 0, HS422_in_ext_comp);
  pwm.setPWM(ID_pouce, 0, HS422_po_inc_comp);
}

void cold_stop()
{
  pwm.setPWM(ID_petitdoigt, 0, 0);
  pwm.setPWM(ID_annulaire, 0, 0);
  pwm.setPWM(ID_majeur, 0, 0);
  pwm.setPWM(ID_index, 0, 0);
  pwm.setPWM(ID_pouce, 0, 0);
}

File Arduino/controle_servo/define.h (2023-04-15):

#define HS422_CNT_SERVO_MIN 120   // Compteur minimum du PWM 12bit du PCA9865 pour le servomoteur HS422 (0°).
#define HS422_CNT_SERVO_MID 307     // Compteur millieu du PWM 12bit du PCA9865 pour le servomoteur HS422 (90°).
#define HS422_CNT_SERVO_MAX 525     // Compteur maximum du PWM 12bit du PCA9865 pour le servomoteur HS422 (180°).
#define HS422_US_MIN  489           // L'équivalent en us du compteur minimum pour le PWM 12bit du PCA9865 pour le servomoteur HS422 (0°).
#define HS422_US_MID  1506          // L'équivalent en us du compteur millieu pour le PWM 12bit du PCA9865 pour le servomoteur HS422 (90°).
#define HS422_US_MAX  2563          // L'équivalent en us du compteur maximum pour le PWM 12bit du PCA9865 pour le servomoteur HS422 (180°).

/* paramètre d'ajustement du module pca9865 */
#define HS422_SERVO_FREQ 50         // Fréquence du PMW pour le servomoteur HS422.
#define PCA9685_OSC_FREQ 25100401   // Fréquence d'oscillation du PCA9865 (Ajusté pour avoir une fréquence de 50Hz précisément).

/* pouce */
#define HS422_po_inc_comp 480       // inclinaison complète
#define HS422_po_inc_init 270       // inclinaison initial
#define HS422_po_ext_comp 250      // extension complète

/* index */
#define HS422_in_inc_comp 320       // inclinaison complète
#define HS422_in_inc_init 130       // inclinaison initial
#define HS422_in_ext_comp 95       // extension complète

/* majeur */
#define HS422_ma_inc_comp 500       // inclinaison complète
#define HS422_ma_inc_init 140       // inclinaison initial
#define HS422_ma_ext_comp 95       // extension complète

/* annulaire */
#define HS422_an_inc_comp 470       // inclinaison complète
#define HS422_an_inc_init 130       // inclinaison initial
#define HS422_an_ext_comp 100       // extension complète

/* petit doigt */
#define HS422_pd_inc_comp 370       // inclinaison complète
#define HS422_pd_inc_init 130       // inclinaison initial
#define HS422_pd_ext_comp 110       // extension complète

/* ID/OUTPUT des doigts sur le PCA9865 */
#define ID_pouce 2                  // moteur ID du pouce
#define ID_index 3                  // moteur ID de l'index
#define ID_majeur 4                 // moteur ID du majeur
#define ID_annulaire 5              // moteur ID annulaire
#define ID_petitdoigt 6             // moteur ID du petit doigt


#define cnt_SERVO_reach 235         // reach
#define cnt_SERVO_half_reach 170    // half reach

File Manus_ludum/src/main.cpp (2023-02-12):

#include <Arduino.h>
#include <Wire.h>
#include <Adafruit_PWMServoDriver.h>
#include "define.h"

// called this way, it uses the default address 0x40
Adafruit_PWMServoDriver pwm = Adafruit_PWMServoDriver();

void setup() {
  Serial.begin(9600);
  Serial.println("8 channel Servo test!");

  pwm.begin();
  pwm.setOscillatorFrequency(PCA9685_OSC_FREQ);
  pwm.setPWMFreq(HS422_SERVO_FREQ);
 
  delay(10);
}


void loop() {
  delay(2000);
  pwm.setPWM(6, 0, HS422_CNT_SERVO_MAX);
  pwm.setPWM(7, 0, HS422_CNT_SERVO_MAX);
  delay(2000);
  pwm.setPWM(6, 0, HS422_CNT_SERVO_MIN);
  pwm.setPWM(7, 0, HS422_CNT_SERVO_MIN);
}

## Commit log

2023-02-12 Code de test pour les servomoteurs
2023-02-15 document ui et py de l'interface et de test
2023-02-21 Supression du git des fichiers inutiles et commentaires
2023-02-21 README.md pour la documentation de l'interface
2023-02-21 Écriture de la coquille du readme
2023-02-21 Mise jour des liens de la table des matières
2023-02-22 Comm. avec controle servo
2023-02-22 changement du port COM et ajout de l'AU
2023-03-02 Ajout CAD
    [Annulaire_DP .stl, Annulaire_MP.stl, Annulaire_PP .stl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]
2023-03-15 Déboguage de la communication
    ajout d'un reset de booléen dans le code Arduino, ménage du code de commworker
    [CommWorker.py, define.h]
2023-03-15 Algorithme de jeux et vision AI
    Première itération de l'algorithme et entraînement et tests du modèle de vision AI
2023-03-22 Essaie d'ajout d'un thread pour la vision
    4h, problème de crash, il reste à débuguer pourquoi ça ne marche pas...
    [algoRPC.py]
2023-03-26 Intégration de la caméra à l'interface
    Algorithme de vision et de jeu, reconnaissance visuelle fonctionnent.
    22-03-2023
    26-03-2023
    8h de travail
2023-03-29 Statistiques et autres fonctionnalités
    Implémentation des statistiques
    Implémentation de l'affichage des données
    Implémentation de la communication des prédictions
    4h - 28/03/2023
2023-04-05 Entraînement d'un modèle et ajustement des stats
2023-04-13 Liste des matériaux et composantes
2023-04-13 Code Arduino
2023-04-14 Ajout de commentaire et chaînes de Markov
    Finalisation du code, dernier débogage et francisation des commentaires
2023-04-14 ajout de la sections sur les librairies
2023-04-15 Code final arduino
2023-04-15 fichier cad
2023-04-15 fichiers cad
2023-04-15 Ajouts des CADs pièces pertinentes
    [Annulaire_DP .stl, Annulaire_DP.step, Annulaire_MP.step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]
2023-04-15 Assemblages finaux
2023-04-15 update CAD
2023-04-15 Dessins assemblage
2023-04-15 Suppression fichiers STL
    [Annulaire_DP .stl, Annulaire_MP.stl, Annulaire_PP .stl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]
2023-04-15 Upload des CAD ligaments
    [Index MCPP Ligament.dxf, Index PPMP Ligament.dxf, Middle MCPP Ligament.dxf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]
2023-04-16 Update Ficchiers CAD
2023-04-16 image doigt insertion
2023-04-16 MCPP ligaments delete
    [Index MCPP Ligament.dxf, Middle MCPP Ligament.dxf, Pinky MCPP Ligament.dxf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]
2023-04-16 Arduino rename
2023-04-16 Changement des noms des fichiers
    Pour faciliter la compréhension du code est des différents fichiers.

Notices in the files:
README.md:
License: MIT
